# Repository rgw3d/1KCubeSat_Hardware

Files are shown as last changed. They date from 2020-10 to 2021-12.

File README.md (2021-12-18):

# 1KCubeSat_Hardware

Hardware design files for my $1000 cubesat.

Schematics & Layouts are done using KiCad V5.1+

## ½ CubeSat

My progress so far, what I'm calling the ½ Cubesat. The [avionics board](avionics_board) is stacked on the [eps board](eps_board)
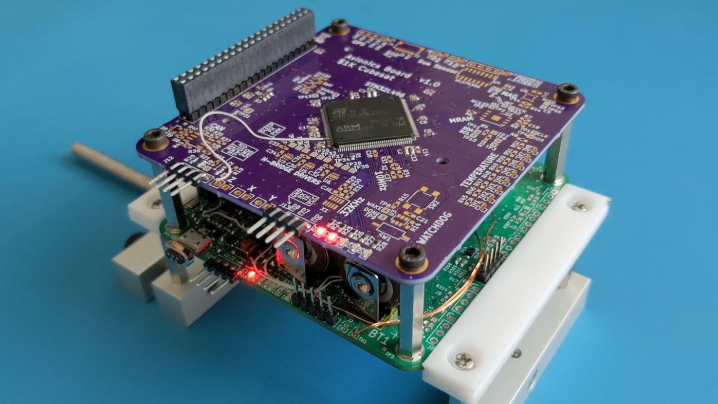
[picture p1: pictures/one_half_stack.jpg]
½ Cubesat Hardware


## Radio Board

See [my fork of the OpenLST repo](https://github.com/rgw3d/openlst-hw/tree/1kcubesat-updates) for more information!
1KCubesat RadioBoard V1

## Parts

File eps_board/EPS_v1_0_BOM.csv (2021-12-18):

Reference | Quantity | Value | Footprint | Datasheet | Mfr. # | Order | Voltage
BT1 BT2 | 2 | Battery_Cell | footprint_custom:BatteryHolder_Keystone_54_v2_1x18650 | https://www.keyelco.com/product.cfm/product_id/826 | 54 | https://www.digikey.com/en/products/detail/keystone-electronics/54/2254090
C1 C2 C13 | 3 | 0.01uF | Capacitor_SMD:C_0603_1608Metric_Pad1.05x0.95mm_HandSolder | ~ | CL10B103KB8NNNC | https://www.digikey.com/en/products/detail/samsung-electro-mechanics/CL10B103KB8NNNC/3886667 | 50V
C4 C5 C6 C7 C8 C9 C10 C11 C12 C16 C17 C18 C19 C20 C21 C24 C26 C29 C31 C36 C38 C47 C49 C50 C53 C55 C57 C58 C61 C63 C65 C66 C69 C71 C73 C74 C77 C79 C81 C82 C85 C87 C89 C90 C93 C95 C97 C98 C101 C103 C105 C106 C109 C111 C113 C114 C117 C119 C121 C122 C125 C127 C129 C130 C133 C135 C137 C138 C141 C143 C145 C146 C149 C151 C153 C154 C157 C159 C161 C162 C165 C167 C169 C170 C173 | 85 | 0.1uF | Capacitor_SMD:C_0603_1608Metric_Pad1.05x0.95mm_HandSolder | ~ | CL10B104KA8NNNC | https://www.digikey.com/product-detail/en/samsung-electro-mechanics/CL10B104KA8NNNC/1276-1006-1-ND/3889092 | 25V
C3 C15 C22 C25 C27 C30 C33 C40 C52 C60 C68 C76 C84 C92 C100 C108 C116 C124 C132 C140 C148 C156 C164 C172 C175 C179 C187 C188 C189 C190 C191 C192 | 32 | 4.7uF | Capacitor_SMD:C_0603_1608Metric_Pad1.05x0.95mm_HandSolder | ~ | C1608X7S1A475K080AC | https://www.digikey.com/product-detail/en/tdk-corporation/C1608X7S1A475K080AC/445-14258-1-ND/3955924 | 10V
C23 C28 C43 C182 | 4 | DNP | Capacitor_SMD:C_0603_1608Metric_Pad1.05x0.95mm_HandSolder | ~
C14 C34 C44 C45 C51 C59 C67 C75 C83 C91 C99 C107 C115 C123 C131 C139 C147 C155 C163 C171 C176 C184 | 22 | 1uF | Capacitor_SMD:C_0603_1608Metric_Pad1.05x0.95mm_HandSolder | ~ | CL10B105KP8NFNC | https://www.digikey.com/product-detail/en/samsung-electro-mechanics/CL10B105KP8NFNC/1276-1945-1-ND/3890031 | 10V
C35 C37 C177 C178 | 4 | 22nF | Capacitor_SMD:C_0603_1608Metric_Pad1.05x0.95mm_HandSolder | ~ | GCM188R72A223KA37D | https://www.digikey.com/product-detail/en/murata-electronics/GCM188R72A223KA37D/490-4782-1-ND/1641701 | 100V
C39 | 1 | 4.7nF | Capacitor_SMD:C_0603_1608Metric_Pad1.05x0.95mm_HandSolder | ~ | 885012206087 | https://www.digikey.com/product-detail/en/w%C3%BCrth-elektronik/885012206087/732-8005-1-ND/5454632 | 50V
C32 C41 C174 C180 C183 C185 | 6 | 47uF | Capacitor_SMD:C_1210_3225Metric_Pad1.42x2.65mm_HandSolder | ~ | GRM32EC81C476KE15L | https://www.digikey.com/product-detail/en/murata-electronics/GRM32EC81C476KE15L/490-10531-1-ND/5026469 | 16V
C42 C181 C186 | 3 | DNP | Capacitor_SMD:C_1210_3225Metric_Pad1.42x2.65mm_HandSolder | ~
C46 C48 C54 C56 C62 C64 C70 C72 C78 C80 C86 C88 C94 C96 C102 C104 C110 C112 C118 C120 C126 C128 C134 C136 C142 C144 C150 C152 C158 C160 C166 C168 | 32 | DNP | Capacitor_SMD:C_0603_1608Metric | ~
D10 D11 D12 D13 D14 D15 D16 D17 | 8 | NRVB120VLSFT1G | footprint_custom:D_SOD-123FL_handsolder | https://www.onsemi.com/pub/Collateral/MBR120VLSFT1-D.PDF | NRVB120VLSFT1G | https://www.digikey.com/product-detail/en/on-semiconductor/NRVB120VLSFT1G/NRVB120VLSFT1GOSCT-ND/8538727
D6 D7 D8 D18 | 4 | ESD9B5.0ST5G | Diode_SMD:D_SOD-923 | https://www.onsemi.com/pub/Collateral/ESD9B-D.PDF | ESD9B5.0ST5G | https://www.digikey.com/product-detail/en/on-semiconductor/ESD9B5-0ST5G/ESD9B5-0ST5GOSCT-ND/1646497
D1 D19 | 2 | LED_SMD_RED | LED_SMD:LED_0603_1608Metric_Pad1.05x0.95mm_HandSolder | https://katalog.we-online.de/led/datasheet/150060RS75000.pdf | 150060RS75000 | https://www.digikey.com/product-detail/en/w%C3%BCrth-elektronik/150060RS75000/732-4978-1-ND/4489899
D2 | 1 | LED_SMD_GREEN | LED_SMD:LED_0603_1608Metric_Pad1.05x0.95mm_HandSolder | https://katalog.we-online.de/led/datasheet/150060VS75000.pdf | 150060VS75000 | https://www.digikey.com/product-detail/en/w%C3%BCrth-elektronik/150060VS75000/732-4980-1-ND/4489904
D3 D4 D5 | 3 | LED_SMD_YELLOW | LED_SMD:LED_0603_1608Metric_Pad1.05x0.95mm_HandSolder | https://www.digikey.com/Web%20Export/Common/icons/datasheet.png | 150060YS75000 | https://www.digikey.com/product-detail/en/w%C3%BCrth-elektronik/150060YS75000/732-4981-1-ND/4489907
D9 | 1 | NUP2105L | Package_TO_SOT_SMD:SOT-23 | http://www.onsemi.com/pub_link/Collateral/NUP2105L-D.PDF | NUP2105LT1G | https://www.digikey.com/product-detail/en/on-semiconductor/NUP2105LT1G/NUP2105LT1GOSCT-ND/1485001
F1 F2 | 2 | Polyfuse | Fuse:Fuse_1206_3216Metric_Pad1.42x1.75mm_HandSolder | ~ | 1206L380SLTHYR | https://www.digikey.com/en/products/detail/littelfuse-inc/1206L380SLTHYR/3305608
FID4 | 1 | Fiducial | Calibration_Scale:Gauge_10mm_Type1_SilkScreenTop | ~
H1 | 1 | MountingHole | MountingHole:MountingHole_2.1mm | ~
H2 H3 H4 H5 | 4 | MountingHole_Pad | MountingHole:MountingHole_3.2mm_M3_Pad_Via | ~
J1 J3 J5 J7 J8 J9 | 6 | Conn_01x04 | Connector_PinHeader_2.54mm:PinHeader_1x04_P2.54mm_Vertical | ~
J12 | 1 | Conn_01x05 | Connector_PinHeader_2.54mm:PinHeader_1x05_P2.54mm_Vertical | ~ | PH1-05-UA | https://www.digikey.com/product-detail/en/adam-tech/PH1-05-UA/2057-PH1-05-UA-ND/9830343
J13 | 1 | Conn_01x04_Male | Connector_PinHeader_2.54mm:PinHeader_1x04_P2.54mm_Vertical | ~ | PREC004SBAN-M71RC | https://www.digikey.com/product-detail/en/sullins-connector-solutions/PREC004SBAN-M71RC/S1112EC-04-ND/2774930
J14 | 1 | USB_B_Micro | Connector_USB:USB_Micro-B_Amphenol_10103594-0001LF_Horizontal | ~ | 10103594-0001LF | https://www.digikey.com/en/products/detail/amphenol-icc-fci/10103594-0001LF/2350351
J2 J4 | 2 | Conn_01x02_Female | Connector_PinHeader_1.27mm:PinHeader_1x02_P1.27mm_Vertical | ~
J6 | 1 | Conn_02x20_Odd_Even | Connector_PinHeader_2.54mm:PinHeader_2x20_P2.54mm_Vertical | ~ | ESQ-120-13-T-D | https://www.digikey.com/product-detail/en/samtec-inc/ESQ-120-13-T-D/ESQ-120-13-T-D-ND/7098677
L1 L2 | 2 | 4.7uH | Inductor_SMD:L_Coilcraft_LPS4018 | ~ | LPS4018-472 | https://www.coilcraft.com/en-us/products/power/shielded-inductors/ferrite-drum/lps/lps4018/
L3 | 1 | 2.2uH | Inductor_SMD:L_Coilcraft_XAL5030 | https://www.coilcraft.com/en-us/products/power/shielded-inductors/molded-inductor/xgl/xgl5030/# | XAL5030-222 | https://www.coilcraft.com/en-us/products/power/shielded-inductors/molded-inductor/xgl/xgl5030/#
Q1 Q2 Q3 Q4 Q5 Q6 Q7 Q8 Q9 Q10 Q11 Q12 Q13 Q14 Q15 Q16 Q17 Q18 Q19 Q20 Q21 Q22 Q23 Q24 Q25 Q26 Q27 Q28 Q29 Q30 Q31 Q32 | 32 | 2N7002K | Package_TO_SOT_SMD:SOT-23 | https://www.diodes.com/assets/Datasheets/ds30896.pdf | 2N7002K-7 | https://www.digikey.com/en/products/detail/diodes-incorporated/2N7002K-7/1934378
R5 R6 R8 R10 R12 R13 R14 R16 R17 R18 R32 R33 R41 R42 R46 R47 R50 R51 R52 R59 R60 R65 R68 R77 R80 R144 R152 R160 R168 R176 R184 R192 R200 R208 R216 R224 R232 R240 R248 R256 R264 R306 R307 R308 R309 R310 R311 R312 R313 R314 R315 R320 | 52 | 100K | Resistor_SMD:R_0603_1608Metric_Pad1.05x0.95mm_HandSolder | ~ | RMCF0603FT100K | https://www.digikey.com/en/products/detail/stackpole-electronics-inc/RMCF0603FT100K/1761112
R101 R103 R105 R123 R125 R127 R129 R135 R137 R139 R141 | 11 | 140K | Resistor_SMD:R_0603_1608Metric_Pad1.05x0.95mm_HandSolder | ~ | RK73H1JTTD1403F | https://www.digikey.com/en/products/detail/koa-speer-electronics-inc/RK73H1JTTD1403F/9845164
R111 R117 | 2 | 698K | Resistor_SMD:R_0603_1608Metric_Pad1.05x0.95mm_HandSolder | ~ | RMCF0603FT698K | https://www.digikey.com/en/products/detail/stackpole-electronics-inc/RMCF0603FT698K/1760941
R113 R115 | 2 | 1.5M | Resistor_SMD:R_0603_1608Metric_Pad1.05x0.95mm_HandSolder | ~ | RC0603FR-071M5L | https://www.digikey.com/en/products/detail/yageo/RC0603FR-071M5L/726865
R15 | 1 | 8.85K | Resistor_SMD:R_0603_1608Metric_Pad1.05x0.95mm_HandSolder | ~ | RMCF0603FT8K87 | https://www.digikey.com/product-detail/en/stackpole-electronics-inc/RMCF0603FT8K87/RMCF0603FT8K87CT-ND/1943053
R19 R20 R21 R22 R23 | 5 | 49.9 | Resistor_SMD:R_0603_1608Metric_Pad1.05x0.95mm_HandSolder | https://www.mouser.com/datasheet/2/392/susumu_RR_Data_Sheet-1206438.pdf | RR0816Q-49R9-D-68R | https://www.mouser.com/ProductDetail/Susumu/RR0816Q-49R9-D-68R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
R322 | 1 | 137K | Resistor_SMD:R_0603_1608Metric_Pad1.05x0.95mm_HandSolder | ~ | RMCF0603FT137K | https://www.digikey.com/en/products/detail/stackpole-electronics-inc/RMCF0603FT137K/1713607
R323 R324 R325 R326 | 4 | 1 | Resistor_SMD:R_0603_1608Metric_Pad1.05x0.95mm_HandSolder | ~ | RK73H1JTTD1R00F | https://www.digikey.com/en/products/detail/koa-speer-electronics-inc/RK73H1JTTD1R00F/9844862
R1 R29 R30 R31 R35 R36 R37 R38 R57 R58 R87 R88 R89 R90 R143 R149 R151 R157 R159 R165 R167 R173 R175 R181 R183 R189 R191 R197 R199 R205 R207 R213 R215 R221 R223 R229 R231 R237 R239 R245 R247 R253 R255 R261 R263 R269 R304 R305 R316 R317 R318 R319 R327 | 53 | 0 | Resistor_SMD:R_0603_1608Metric_Pad1.05x0.95mm_HandSolder | ~ | RK73Z1JTTD | https://www.digikey.com/product-detail/en/koa-speer-electronics-inc/RK73Z1JTTD/2019-RK73Z1JTTDCT-ND/9847522
R24 R25 R26 R27 R28 R329 | 6 | 330 | Resistor_SMD:R_0603_1608Metric_Pad1.05x0.95mm_HandSolder | https://www.mouser.com/datasheet/2/427/dcrcwe3-1762152.pdf | CRCW0603330RJNEA | https://www.mouser.com/ProductDetail/Vishay-Dale/CRCW0603330RJNEA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
R39 R40 | 2 | 60.4 | Resistor_SMD:R_0603_1608Metric_Pad1.05x0.95mm_HandSolder | ~ | RMCF0603FT60R4 | https://www.digikey.com/product-detail/en/stackpole-electronics-inc/RMCF0603FT60R4/RMCF0603FT60R4CT-ND/2418105
R34 R43 | 2 | 150K | Resistor_SMD:R_0603_1608Metric_Pad1.05x0.95mm_HandSolder | ~ | RMCF0603FT150K | https://www.digikey.com/en/products/detail/stackpole-electronics-inc/RMCF0603FT150K/1761318
R11 R48 R62 R64 R66 R67 R74 R76 R78 R79 R97 R98 | 12 | 10K | Resistor_SMD:R_0603_1608Metric_Pad1.05x0.95mm_HandSolder | ~ | RMCF0603FT10K0 | https://www.digikey.com/en/products/detail/stackpole-electronics-inc/RMCF0603FT10K0/1761235
R2 R3 R4 R7 R49 R53 R54 R55 R56 R328 | 10 | 10m | Resistor_SMD:R_0603_1608Metric_Pad1.05x0.95mm_HandSolder | ~ | ERJ-3LWJR010V | https://www.digikey.com/product-detail/en/panasonic-electronic-components/ERJ-3LWJR010V/P19190CT-ND/6004545
R61 R73 | 2 | 26.7K | Resistor_SMD:R_0603_1608Metric_Pad1.05x0.95mm_HandSolder | ~ | RK73H1JTTD2672F | https://www.digikey.com/en/products/detail/koa-speer-electronics-inc/RK73H1JTTD2672F/9845116
R63 R71 R75 R83 R145 R147 R148 R153 R155 R156 R161 R163 R164 R169 R171 R172 R177 R179 R180 R185 R187 R188 R193 R195 R196 R201 R203 R204 R209 R211 R212 R217 R219 R220 R225 R227 R228 R233 R235 R236 R241 R243 R244 R249 R251 R252 R257 R259 R260 R265 R267 R268 R321 | 53 | 1M | Resistor_SMD:R_0603_1608Metric_Pad1.05x0.95mm_HandSolder | ~ | RMCF0603JT1M00 | https://www.digikey.com/en/products/detail/stackpole-electronics-inc/RMCF0603JT1M00/1758066
R69 R81 | 2 | 280K | Resistor_SMD:R_0603_1608Metric_Pad1.05x0.95mm_HandSolder | ~ | RMCF0603FT280K | https://www.digikey.com/en/products/detail/stackpole-electronics-inc/RMCF0603FT280K/1761337
R70 R82 R150 R158 R166 R174 R182 R190 R198 R206 R214 R222 R230 R238 R246 R254 R262 R270 | 18 | DNP | Resistor_SMD:R_0603_1608Metric_Pad1.05x0.95mm_HandSolder | ~
R72 R84 R100 R102 R104 R106 R112 R114 R116 R118 R124 R126 R128 R130 R136 R138 R140 R142 | 18 | 3.09K | Resistor_SMD:R_0603_1608Metric_Pad1.05x0.95mm_HandSolder | ~ | RMCF0603FT3K09 | https://www.digikey.com/en/products/detail/stackpole-electronics-inc/RMCF0603FT3K09/1761340
R85 R86 | 2 | 150 | Resistor_SMD:R_0603_1608Metric_Pad1.05x0.95mm_HandSolder | ~ | RMCF0603JT150R | https://www.digikey.com/en/products/detail/stackpole-electronics-inc/RMCF0603JT150R/1757965
R9 | 1 | 224K | Resistor_SMD:R_0603_1608Metric_Pad1.05x0.95mm_HandSolder | ~ | RMCF0603FT221K | https://www.digikey.com/en/products/detail/stackpole-electronics-inc/RMCF0603FT221K/1760806
R91 R92 | 2 | 1K | Resistor_SMD:R_0603_1608Metric_Pad1.05x0.95mm_HandSolder | ~ | RMCF0603FT1K00 | https://www.digikey.com/en/products/detail/stackpole-electronics-inc/RMCF0603FT1K00/1761077
R93 R95 R96 R107 R108 R109 R110 R119 R120 R121 R122 R131 R132 R133 R134 | 15 | 0.1 | Resistor_SMD:R_0603_1608Metric_Pad1.05x0.95mm_HandSolder | ~ | ERJ-3RSFR10V | https://www.digikey.com/product-detail/en/panasonic-electronic-components/ERJ-3RSFR10V/P-10AJCT-ND/308098
R94 | 1 | 0.039 | Resistor_SMD:R_0603_1608Metric_Pad1.05x0.95mm_HandSolder | ~ | ERJ-3BWFR039V | https://www.digikey.com/en/products/detail/panasonic-electronic-components/ERJ-3BWFR039V/5647502
R99 | 1 | 20K | Resistor_SMD:R_0603_1608Metric_Pad1.05x0.95mm_HandSolder | ~ | RMCF0603FT20K0 | https://www.digikey.com/en/products/detail/stackpole-electronics-inc/RMCF0603FT20K0/1760829
SW1 | 1 | SW_DIP_x01 | Button_Switch_SMD:SW_DIP_SPSTx01_Slide_Copal_CHS-01B_W7.62mm_P1.27mm | https://www.nidec-copal-electronics.com/e/catalog/switch/chs.pdf | CHS-01TB | https://www.digikey.com/product-detail/en/nidec-copal-electronics/CHS-01TB/563-1004-1-ND/948403
SW2 | 1 | SW_Push | Button_Switch_SMD:SW_SPST_TL3305A | https://sten-eswitch-13110800-production.s3.amazonaws.com/system/asset/product_line/data_sheet/213/TL3305.pdf | TL3305AF260QG | https://www.digikey.com/product-detail/en/e-switch/TL3305AF260QG/EG5353CT-ND/5816198
TH1 TH2 | 2 | Thermistor_NTC | Connector_PinHeader_1.27mm:PinHeader_1x02_P1.27mm_Vertical | ~ | NXFT15XH103FA2B130 | https://www.digikey.com/en/products/detail/murata-electronics/NXFT15XH103FA2B130/3863299
TP37 TP39 | 2 | TP_1.5x1.5 | TestPoint:TestPoint_THTPad_1.0x1.0mm_Drill0.5mm | ~
TP7 TP10 TP11 TP12 TP13 TP14 TP15 TP16 TP17 TP18 TP19 TP20 | 12 | TP_1x1 | TestPoint:TestPoint_THTPad_1.0x1.0mm_Drill0.5mm | ~
TP1 TP2 TP3 TP4 TP5 TP8 TP9 | 7 | TP_smt_1x1 | TestPoint:TestPoint_THTPad_1.0x1.0mm_Drill0.5mm | ~
U1 | 1 | STM32L496ZGTx | Package_QFP:LQFP-144_20x20mm_P0.5mm | http://www.st.com/st-web-ui/static/active/en/resource/technical/document/datasheet/DM00284211.pdf | STM32L496ZGT3 | https://www.digikey.com/product-detail/en/stmicroelectronics/STM32L496ZGT3/497-17177-ND/6709882
U10 U13 | 2 | MCP65R46 | Package_TO_SOT_SMD:SOT-23-6_Handsoldering | http://ww1.microchip.com/downloads/en/DeviceDoc/22269B.pdf | MCP65R46T-2402E/CHY | https://www.digikey.com/product-detail/en/microchip-technology/MCP65R46T-2402E-CHY/MCP65R46T-2402E-CHYCT-ND/2618485
U11 U14 U22 U26 U30 U34 U38 U42 U46 U50 U54 U58 U62 U66 U70 U74 U78 U82 | 18 | FPF2123 | Package_TO_SOT_SMD:SOT-23-5_HandSoldering | https://www.onsemi.com/pub/Collateral/FPF2125-D.pdf | FPF2123 | https://www.digikey.com/product-detail/en/on-semiconductor/FPF2123/FPF2123CT-ND/1033703
U15 | 1 | LTC4415 | footprint_custom:MSOP-16-1EP_3x4.039mm_P0.5mm_EP1.651x2.845mm_0.3mmThermalVias | https://www.analog.com/media/en/technical-documentation/data-sheets/4415fa.pdf | LTC4415EMSE#PBF | https://www.digikey.com/product-detail/en/analog-devices-inc/LTC4415EMSE-PBF/LTC4415EMSE-PBF-ND/2769860
U16 U83 | 2 | LTC3130-1 | footprint_custom:MSOP-16-1EP_3x4.039mm_P0.5mm_EP1.651x2.845mm_0.3mmThermalVias | https://www.analog.com/media/en/technical-documentation/data-sheets/3130f.pdf | LTC3130EMSE-1#PBF | https://www.digikey.com/product-detail/en/analog-devices-inc/LTC3130EMSE-1-PBF/LTC3130EMSE-1-PBF-ND/6174043
U19 U23 U27 U31 U35 U39 U43 U47 U51 U55 U59 U63 U67 U71 U75 U79 | 16 | NCS211 | Package_TO_SOT_SMD:SOT-363_SC-70-6 | https://www.onsemi.com/pub/Collateral/NCS210R-D.PDF | NCS214RSQT2G | https://www.digikey.com/product-detail/en/on-semiconductor/NCS214RSQT2G/NCS214RSQT2GOSCT-ND/9749437
U2 | 1 | MR25H10 | Package_DFN_QFN:DFN-8-1EP_6x5mm_P1.27mm_EP2x2mm | https://media.digikey.com/pdf/Data%20Sheets/EverSpin%20Technologies/MR25H40_Datasheet_Rev6.pdf | MR25H10MDF | https://www.digikey.com/product-detail/en/everspin-technologies-inc/MR25H10MDF/819-1042-ND/4047457
U20 U24 U28 U32 U36 U40 U44 U48 U52 U56 U60 U64 U68 U72 U76 U80 | 16 | 74LVC1G07 | Package_TO_SOT_SMD:SOT-353_SC-70-5 | https://assets.nexperia.com/documents/data-sheet/74LVC1G07.pdf | 74LVC1G07GW,125 | https://www.digikey.com/product-detail/en/nexperia-usa-inc/74LVC1G07GW-125/1727-3099-1-ND/946756
U21 U25 U29 U33 U37 U41 U45 U49 U53 U57 U61 U65 U69 U73 U77 U81 | 16 | MCP65R46 | Package_TO_SOT_SMD:SOT-23-6 | http://ww1.microchip.com/downloads/en/DeviceDoc/22269B.pdf | MCP65R46T-2402E/CHY | https://www.digikey.com/product-detail/en/microchip-technology/MCP65R46T-2402E-CHY/MCP65R46T-2402E-CHYCT-ND/2618485
U3 | 1 | TPL5010 | Package_TO_SOT_SMD:SOT-23-6 | http://www.ti.com/lit/ds/symlink/tpl5010.pdf | TPL5010DDCR | https://www.digikey.com/product-detail/en/texas-instruments/TPL5010DDCR/296-44392-1-ND/6110660
U4 U5 U17 U18 | 4 | TPS270 | Package_TO_SOT_SMD:TSOT-23-6_HandSoldering | https://www.ti.com/lit/ds/symlink/tps27081a.pdf?HQS=TI-null-null-digikeymode-df-pf-null-wwe&ts=1599272332553 | TPS27081ADDCR | https://www.digikey.com/product-detail/en/texas-instruments/TPS27081ADDCR/296-34970-1-ND/3671576
U6 U7 | 2 | 74LVC1G07 | Package_TO_SOT_SMD:SOT-353_SC-70-5_Handsoldering | http://www.ti.com/lit/sg/scyt129e/scyt129e.pdf | 74LVC1G07GW,125 | https://www.digikey.com/product-detail/en/nexperia-usa-inc/74LVC1G07GW-125/1727-3099-1-ND/946756
U8 | 1 | SN65HVD230 | Package_SO:SOIC-8_3.9x4.9mm_P1.27mm | http://www.ti.com/lit/ds/symlink/sn65hvd230.pdf | SN65HVD230QDRG4Q1 | https://www.digikey.com/product-detail/en/texas-instruments/SN65HVD230QDG4/296-26342-5-ND/1900402
U84 | 1 | MP3414A | Package_TO_SOT_SMD:TSOT-23-8_HandSoldering | https://www.monolithicpower.com/en/documentview/productdocument/index/version/2/document_type/Datasheet/lang/en/sku/MP3414A/document_id/1172/ | MP3414AGJ-Z | https://www.digikey.com/en/products/detail/monolithic-power-systems-inc/MP3414AGJ-Z/7361472
U9 U12 | 2 | LTC4066 | footprint_custom:QFN-24-1EP_4x4mm_P0.5mm_EP2.6x2.6mm_0.4mmThermalVias | https://www.analog.com/media/en/technical-documentation/data-sheets/4066fc.pdf | LTC4066EUF#PBF | https://www.digikey.com/product-detail/en/analog-devices-inc/LTC4066EUF-PBF/LTC4066EUF-PBF-ND/1746224
X1 | 1 | TG-3541CE | footprint_custom:Oscillator_SMD_SeikoEpson_TG3541CE-10Pin_3.2x2.5mm_HandSoldering | https://support.epson.biz/td/api/doc_check.php?dl=brief_TG-3541CE&lang=en | TG-3541CE 32.7680KXA3 | https://www.digikey.com/product-detail/en/epson/TG-3541CE-32-7680KXA3/SER4421CT-ND/10239844

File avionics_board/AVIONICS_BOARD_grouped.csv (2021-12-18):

Reference | Quantity | Value | Footprint | Datasheet | Mfr. # | Order | Voltage | Alt
C1 C2 C13 | 3 | 0.01uF | Capacitor_SMD:C_0603_1608Metric_Pad1.08x0.95mm_HandSolder | ~ | CL10B103KB8NNNC | https://www.digikey.com/en/products/detail/samsung-electro-mechanics/CL10B103KB8NNNC/3886667 | 50V
C14 C28 C44 | 3 | 1uF | Capacitor_SMD:C_0603_1608Metric_Pad1.08x0.95mm_HandSolder | ~ | CL10B105KP8NFNC | https://www.digikey.com/product-detail/en/samsung-electro-mechanics/CL10B105KP8NFNC/1276-1945-1-ND/3890031 | 10V
C3 C15 | 2 | 4.7uF | Capacitor_SMD:C_0603_1608Metric_Pad1.08x0.95mm_HandSolder | ~ | C1608X7S1A475K080AC | https://www.digikey.com/product-detail/en/tdk-corporation/C1608X7S1A475K080AC/445-14258-1-ND/3955924 | 10V
C39 | 1 | 4.7nF | Capacitor_SMD:C_0603_1608Metric_Pad1.08x0.95mm_HandSolder | ~ | 885012206087 | https://www.digikey.com/product-detail/en/w%C3%BCrth-elektronik/885012206087/732-8005-1-ND/5454632 | 50V
C45 | 1 | 10uF | Capacitor_SMD:C_0603_1608Metric_Pad1.08x0.95mm_HandSolder | ~ | CL10X106MO8NRNC | https://www.digikey.com/product-detail/en/samsung-electro-mechanics/CL10X106MO8NRNC/1276-6769-1-ND/5961628 | 16V
C4 C5 C6 C7 C8 C9 C10 C11 C12 C16 C17 C18 C19 C20 C21 C29 C30 C31 C32 C33 C34 C35 C36 C37 C38 C40 C43 | 27 | 0.1uF | Capacitor_SMD:C_0603_1608Metric_Pad1.08x0.95mm_HandSolder | ~ | CL10B104KA8NNNC | https://www.digikey.com/product-detail/en/samsung-electro-mechanics/CL10B104KA8NNNC/1276-1006-1-ND/3889092 | 25V
D1 | 1 | LED_SMD_RED | LED_SMD:LED_0603_1608Metric_Pad1.05x0.95mm_HandSolder | https://katalog.we-online.de/led/datasheet/150060RS75000.pdf | 150060RS75000 | https://www.digikey.com/product-detail/en/w%C3%BCrth-elektronik/150060RS75000/732-4978-1-ND/4489899
D2 | 1 | LED_SMD_GREEN | LED_SMD:LED_0603_1608Metric_Pad1.05x0.95mm_HandSolder | https://katalog.we-online.de/led/datasheet/150060VS75000.pdf | 150060VS75000 | https://www.digikey.com/product-detail/en/w%C3%BCrth-elektronik/150060VS75000/732-4980-1-ND/4489904
D3 D4 D5 | 3 | LED_SMD_YELLOW | LED_SMD:LED_0603_1608Metric_Pad1.05x0.95mm_HandSolder | https://www.digikey.com/Web%20Export/Common/icons/datasheet.png | 150060YS75000 | https://www.digikey.com/product-detail/en/w%C3%BCrth-elektronik/150060YS75000/732-4981-1-ND/4489907
D6 D7 D8 | 3 | ESD9B5.0ST5G | Diode_SMD:D_SOD-923 | https://www.onsemi.com/pub/Collateral/ESD9B-D.PDF | ESD9B5.0ST5G | https://www.digikey.com/product-detail/en/on-semiconductor/ESD9B5-0ST5G/ESD9B5-0ST5GOSCT-ND/1646497
D9 | 1 | NUP2105L | Package_TO_SOT_SMD:SOT-23 | http://www.onsemi.com/pub_link/Collateral/NUP2105L-D.PDF | NUP2105LT1G | https://www.digikey.com/product-detail/en/on-semiconductor/NUP2105LT1G/NUP2105LT1GOSCT-ND/1485001
H1 H2 H3 H4 | 4 | MountingHole_Pad | MountingHole:MountingHole_3.2mm_M3_Pad_Via | ~
H5 H6 H7 | 3 | MountingHole | MountingHole:MountingHole_2.7mm | ~
J1 | 1 | Conn_02x20_Odd_Even | Connector_PinHeader_2.54mm:PinHeader_2x20_P2.54mm_Vertical | ~ | ESQ-120-13-T-D | https://www.digikey.com/product-detail/en/samtec-inc/ESQ-120-13-T-D/ESQ-120-13-T-D-ND/7098677
J13 | 1 | Conn_01x04_Male | Connector_PinHeader_2.54mm:PinHeader_1x04_P2.54mm_Vertical | ~ | PREC004SBAN-M71RC | https://www.digikey.com/product-detail/en/sullins-connector-solutions/PREC004SBAN-M71RC/S1112EC-04-ND/2774930
J3 | 1 | JST socket 6-pin 1mm pitch JST SH SM06B-SRSS-TB | Connector_JST:JST_SH_SM06B-SRSS-TB_1x06-1MP_P1.00mm_Horizontal | ~ | SM06B-SRSS-TB(LF)(SN) | https://www.digikey.com/product-detail/en/jst-sales-america-inc/SM06B-SRSS-TB-LF-SN/455-1806-1-ND/926877
J4 J7 J12 | 3 | Conn_01x05 | Connector_PinHeader_2.54mm:PinHeader_1x05_P2.54mm_Vertical | ~ | PH1-05-UA | https://www.digikey.com/product-detail/en/adam-tech/PH1-05-UA/2057-PH1-05-UA-ND/9830343
J5 J6 J9 J10 J11 | 5 | Conn_01x02 | Connector_PinHeader_2.54mm:PinHeader_1x02_P2.54mm_Vertical | ~ | PREC002SAAN-RC | https://www.digikey.com/product-detail/en/sullins-connector-solutions/PREC002SAAN-RC/S1012EC-02-ND/2774852
R1 R8 R16 R17 R18 R29 R30 R31 R32 R33 R34 R35 R36 R37 R38 R42 R43 R44 | 18 | 0 | Resistor_SMD:R_0603_1608Metric_Pad0.98x0.95mm_HandSolder | ~ | RK73Z1JTTD | https://www.digikey.com/product-detail/en/koa-speer-electronics-inc/RK73Z1JTTD/2019-RK73Z1JTTDCT-ND/9847522
R9 R10 R11 R12 | 4 | DNP | Resistor_SMD:R_0603_1608Metric_Pad0.98x0.95mm_HandSolder | ~
R15 | 1 | 8.85K | Resistor_SMD:R_0603_1608Metric_Pad0.98x0.95mm_HandSolder | ~ | RMCF0603FT8K87 | https://www.digikey.com/product-detail/en/stackpole-electronics-inc/RMCF0603FT8K87/RMCF0603FT8K87CT-ND/1943053
R2 R3 R4 R7 | 4 | 10m | Resistor_SMD:R_0603_1608Metric_Pad0.98x0.95mm_HandSolder | ~ | ERJ-3LWJR010V | https://www.digikey.com/product-detail/en/panasonic-electronic-components/ERJ-3LWJR010V/P19190CT-ND/6004545
R19 R20 R21 R22 R23 | 5 | 49.9 | Resistor_SMD:R_0603_1608Metric_Pad0.98x0.95mm_HandSolder | https://www.mouser.com/datasheet/2/392/susumu_RR_Data_Sheet-1206438.pdf | RR0816Q-49R9-D-68R | https://www.mouser.com/ProductDetail/Susumu/RR0816Q-49R9-D-68R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
R24 R25 R26 R27 R28 | 5 | 330 | Resistor_SMD:R_0603_1608Metric_Pad0.98x0.95mm_HandSolder | https://www.mouser.com/datasheet/2/427/dcrcwe3-1762152.pdf | CRCW0603330RJNEA | https://www.mouser.com/ProductDetail/Vishay-Dale/CRCW0603330RJNEA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
R39 R40 | 2 | 60.4 | Resistor_SMD:R_0603_1608Metric_Pad0.98x0.95mm_HandSolder | ~ | RMCF0603FT60R4 | https://www.digikey.com/product-detail/en/stackpole-electronics-inc/RMCF0603FT60R4/RMCF0603FT60R4CT-ND/2418105
R45 R46 R47 R48 R49 R50 R51 R52 | 8 | 47K | Resistor_SMD:R_0603_1608Metric_Pad0.98x0.95mm_HandSolder | https://www.bourns.com/docs/Product-Datasheets/CHPREZTR.pdf | CR0603-FX-4702ELF | https://www.digikey.com/product-detail/en/bourns-inc/CR0603-FX-4702ELF/CR0603-FX-4702ELFCT-ND/3925317
R5 R6 R14 R41 | 4 | 100K | Resistor_SMD:R_0603_1608Metric_Pad0.98x0.95mm_HandSolder | ~ | RMCF0603FT100K | https://www.digikey.com/en/products/detail/stackpole-electronics-inc/RMCF0603FT100K/1761112
SW1 | 1 | SW_DIP_x01 | Button_Switch_SMD:SW_DIP_SPSTx01_Slide_Copal_CHS-01B_W7.62mm_P1.27mm | https://www.nidec-copal-electronics.com/e/catalog/switch/chs.pdf | CHS-01TB | https://www.digikey.com/product-detail/en/nidec-copal-electronics/CHS-01TB/563-1004-1-ND/948403
SW2 | 1 | SW_Push | Button_Switch_SMD:SW_SPST_TL3305A | https://sten-eswitch-13110800-production.s3.amazonaws.com/system/asset/product_line/data_sheet/213/TL3305.pdf | TL3305AF260QG | https://www.digikey.com/product-detail/en/e-switch/TL3305AF260QG/EG5353CT-ND/5816198
TH1 TH2 TH3 TH4 TH5 TH6 TH7 TH8 | 8 | Thermistor_NTC | Connector_PinHeader_1.27mm:PinHeader_1x02_P1.27mm_Vertical | https://www.murata.com/~/media/webrenewal/support/library/catalog/products/thermistor/ntc/r44e.ashx?la=en-us | NXFT15WB473FA2B150 | https://www.digikey.com/product-detail/en/murata-electronics/NXFT15WB473FA2B150/490-14853-ND/6606459
TP7 TP10 TP11 TP12 TP13 | 5 | TP_tht_1x1 | TestPoint:TestPoint_THTPad_1.0x1.0mm_Drill0.5mm | ~
TP14 TP15 TP16 TP26 TP27 TP28 TP29 TP30 TP33 TP34 TP35 TP36 TP43 TP44 TP45 TP48 TP49 TP50 TP52 TP53 TP54 TP56 TP57 | 23 | TP_smt_1x1 | TestPoint:TestPoint_Pad_1.0x1.0mm | ~
TP1 TP2 TP3 TP4 TP5 TP6 TP8 TP9 | 8 | TP_smt_1x1 | TestPoint:TestPoint_THTPad_1.0x1.0mm_Drill0.5mm | ~
TP31 TP32 | 2 | TP_1.5x1.5 | TestPoint:TestPoint_THTPad_1.5x1.5mm_Drill0.7mm | ~
TP37 TP39 | 2 | TP_1.5x1.5 | TestPoint:TestPoint_THTPad_1.0x1.0mm_Drill0.5mm | ~
U1 | 1 | STM32L496ZGTx | Package_QFP:LQFP-144_20x20mm_P0.5mm | http://www.st.com/st-web-ui/static/active/en/resource/technical/document/datasheet/DM00284211.pdf | STM32L496ZGT3 | https://www.digikey.com/product-detail/en/stmicroelectronics/STM32L496ZGT3/497-17177-ND/6709882
U10 | 1 | BMG250 | Package_LGA:Bosch_LGA-14_3x2.5mm_P0.5mm | https://ae-bst.resource.bosch.com/media/_tech/media/datasheets/BST-BMG250-DS000.pdf | BMG250 | https://www.digikey.com/product-detail/en/bosch-sensortec/BMG250/828-1065-1-ND/6187900
U11 U12 | 2 | 74LVC1G07 | Package_TO_SOT_SMD:SOT-353_SC-70-5_Handsoldering | http://www.ti.com/lit/sg/scyt129e/scyt129e.pdf | 74LVC1G07GW,125 | https://www.digikey.com/product-detail/en/nexperia-usa-inc/74LVC1G07GW-125/1727-3099-1-ND/946756 |  | https://www.digikey.com/product-detail/en/texas-instruments/SN74LVC1G07DCKR/296-8486-1-ND/377456
U2 | 1 | MR25H10 | Package_DFN_QFN:DFN-8-1EP_6x5mm_P1.27mm_EP2x2mm | https://media.digikey.com/pdf/Data%20Sheets/EverSpin%20Technologies/MR25H40_Datasheet_Rev6.pdf | MR25H10MDF | https://www.digikey.com/product-detail/en/everspin-technologies-inc/MR25H10MDF/819-1042-ND/4047457
U3 | 1 | TPL5010 | Package_TO_SOT_SMD:SOT-23-6 | http://www.ti.com/lit/ds/symlink/tpl5010.pdf | TPL5010DDCR | https://www.digikey.com/product-detail/en/texas-instruments/TPL5010DDCR/296-44392-1-ND/6110660
U4 | 1 | MLX75306 | Package_SO:SOIC-16_3.9x9.9mm_P1.27mm |  | MLX75306KXZ-BAA-000-RE | https://www.digikey.com/product-detail/en/melexis-technologies-nv/MLX75306KXZ-BAA-000-RE/MLX75306KXZ-BAA-000-RECT-ND/3640931
U5 U6 U7 | 3 | DRV8838 | Package_SON:WSON-8-1EP_2x2mm_P0.5mm_EP0.9x1.6mm | http://www.ti.com/lit/ds/symlink/drv8837.pdf | DRV8838DSGR | https://www.digikey.com/product-detail/en/texas-instruments/DRV8838DSGR/296-40081-1-ND/5177958
U8 | 1 | SN65HVD230 | Package_SO:SOIC-8_3.9x4.9mm_P1.27mm | http://www.ti.com/lit/ds/symlink/sn65hvd230.pdf | SN65HVD230QDRG4Q1 | https://www.digikey.com/product-detail/en/texas-instruments/SN65HVD230QDG4/296-26342-5-ND/1900402
U9 | 1 | MMC5983MA | Package_LGA:LGA-16_3x3mm_P0.5mm | https://media.digikey.com/pdf/Data%20Sheets/MEMSIC%20PDFs/MMC5983MA_RevA_4-3-19.pdf | MMC5983MA | https://www.digikey.com/product-detail/en/memsic-inc/MMC5983MA/1267-MMC5983MACT-ND/10452801
X1 | 1 | TG-3541CE | footprint_custom:Oscillator_SMD_SeikoEpson_TG3541CE-10Pin_3.2x2.5mm_HandSoldering | https://support.epson.biz/td/api/doc_check.php?dl=brief_TG-3541CE&lang=en | TG-3541CE 32.7680KXA3 | https://www.digikey.com/product-detail/en/epson/TG-3541CE-32-7680KXA3/SER4421CT-ND/10239844
X2 | 1 | ECS-TXO-2016 | footprint_custom:Oscillator_SMD_ECS_TXO-2016-xx-xxx-4Pin_2.0x1.6mm | https://ecsxtal.com/store/pdf/ECS-TXO-2016.pdf | ECS-TXO-2016-33-100-TR | https://www.digikey.com/product-detail/en/ecs-inc/ECS-TXO-2016-33-100-TR/XC3159CT-ND/10244142

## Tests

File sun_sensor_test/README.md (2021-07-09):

# Sun Sensor Test

Testing out a potential sun sensor using the K857PE 4-Quadrent Photodiode. See the [pdf](https://raw.githubusercontent.com/rgw3d/1KCubeSat_Hardware/master/sun_sensor_test/sun_sensor_test.pdf) for more information.

See [my video on this board](https://www.youtube.com/watch?v=8ttuiI6RIH0) for more information.

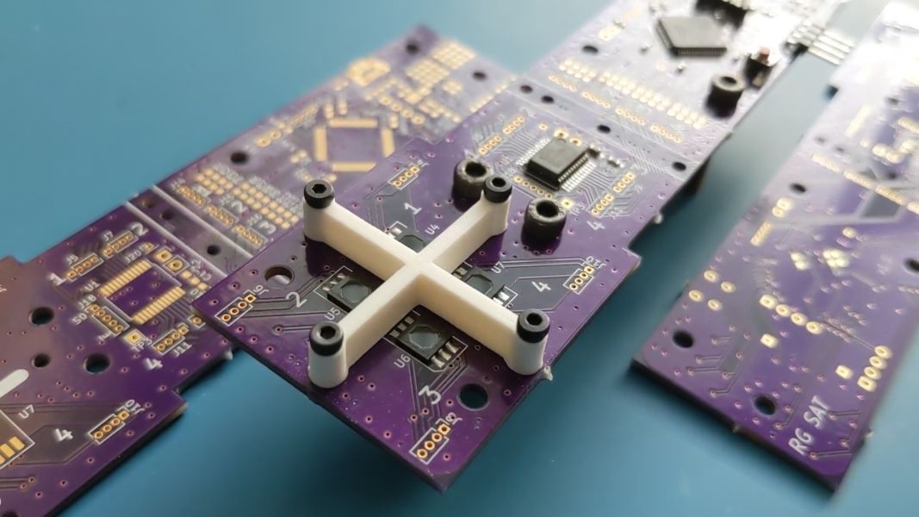
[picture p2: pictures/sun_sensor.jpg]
Sun Sensor Hardware


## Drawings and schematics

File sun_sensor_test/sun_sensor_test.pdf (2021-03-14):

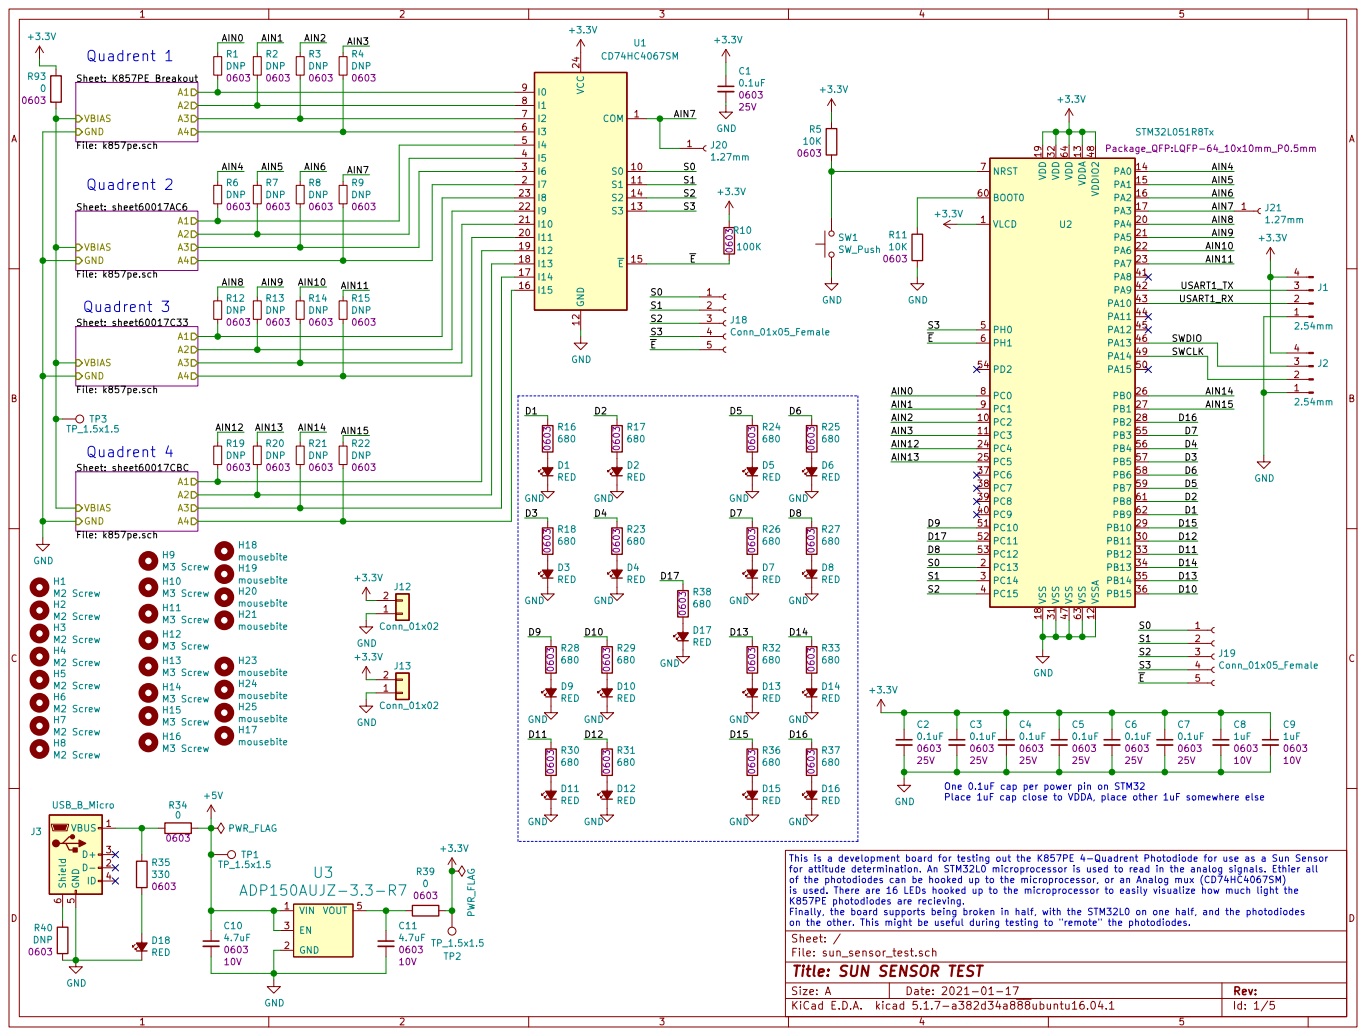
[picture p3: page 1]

Sheet: K857PE Breakout File: k857pe.sch GND
A1A2A3A4 VBIAS
25V H6M2 Screw

Sheet: sheet60017AC6 File: k857pe.sch GND

Quadrent 3
Sheet: sheet60017C33 File: k857pe.sch GND

One 0.1uF cap per power pin on STM32
Place 1uF cap close to VDDA, place other 1uF somewhere else

for attitude determination. An STM32L0 microprocessor is used to read in the analog signals. Ethier all
of the photodiodes can be hooked up to the microprocessor, or an Analog mux (CD74HC4067SM)
is used. There are 16 LEDs hooked up to the microprocessor to easily visualize how much light the
K857PE photodiodes are recieving.
Finally, the board supports being broken in half, with the STM32L0 on one half, and the photodiodes
on the other. This might be useful during testing to "remote" the photodiodes.
File: sun_sensor_test.sch Sheet: /
Id: 1/5 Title: SUN SENSOR TEST

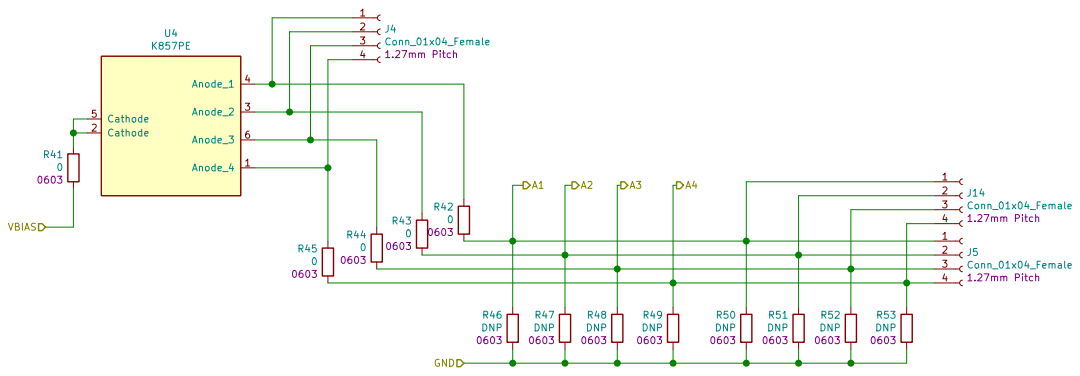
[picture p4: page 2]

File: k857pe.sch Sheet: /K857PE Breakout/
Id: 2/5 Title: K857PE

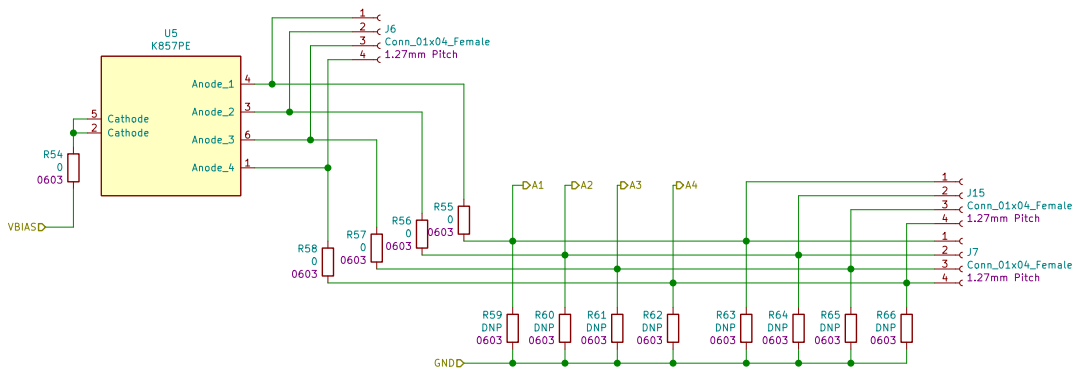
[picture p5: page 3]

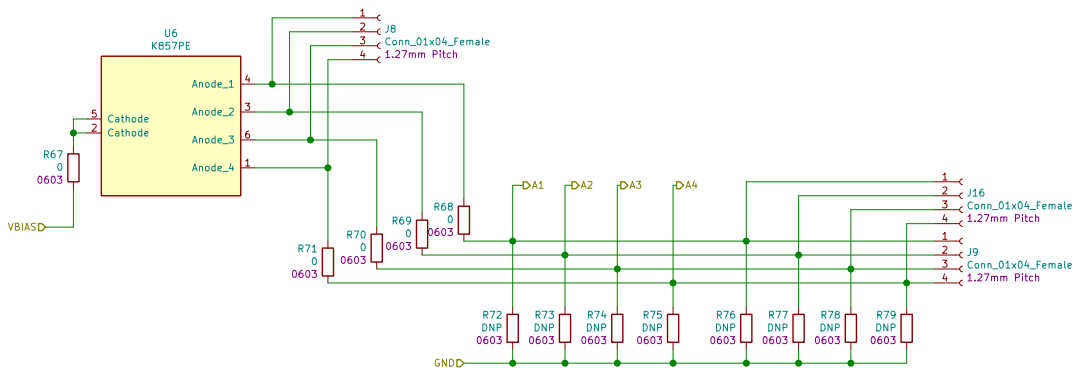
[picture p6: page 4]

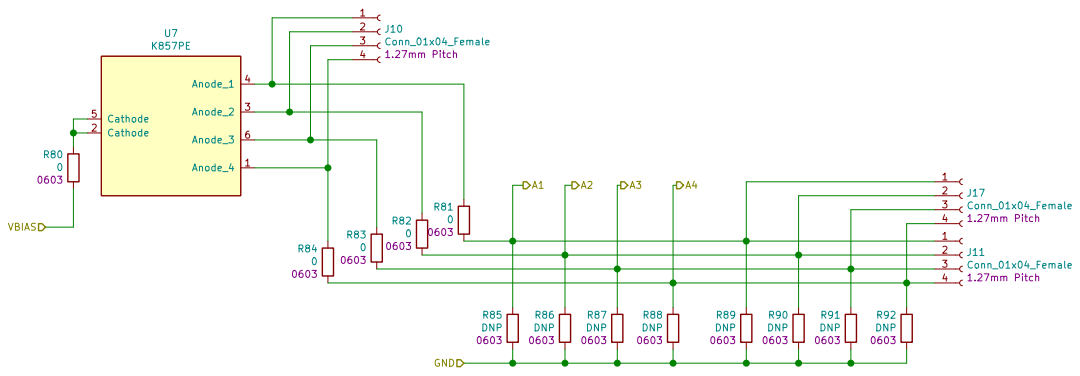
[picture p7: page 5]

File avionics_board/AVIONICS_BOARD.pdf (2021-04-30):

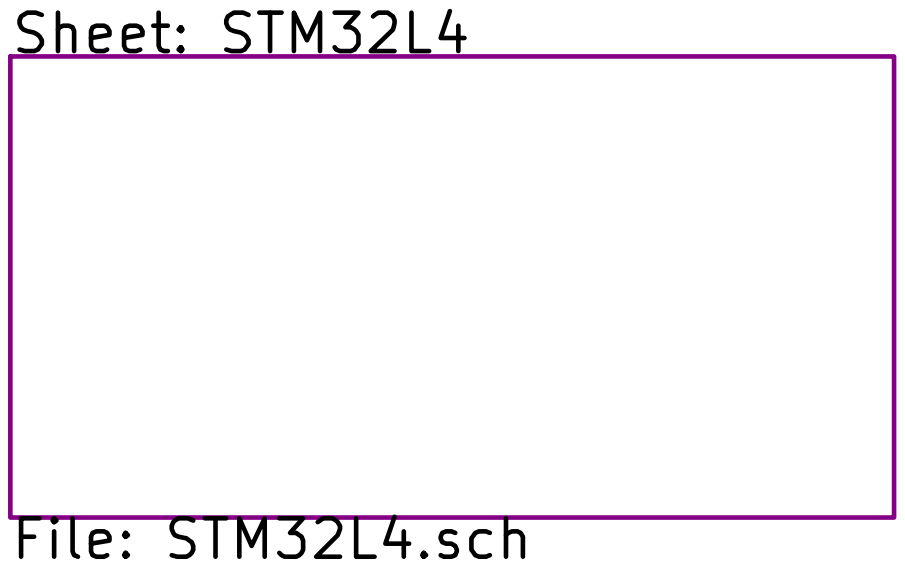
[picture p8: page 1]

File: AVIONICS_BOARD.sch Sheet: / Sheet: STM32L4 File: STM32L4.sch

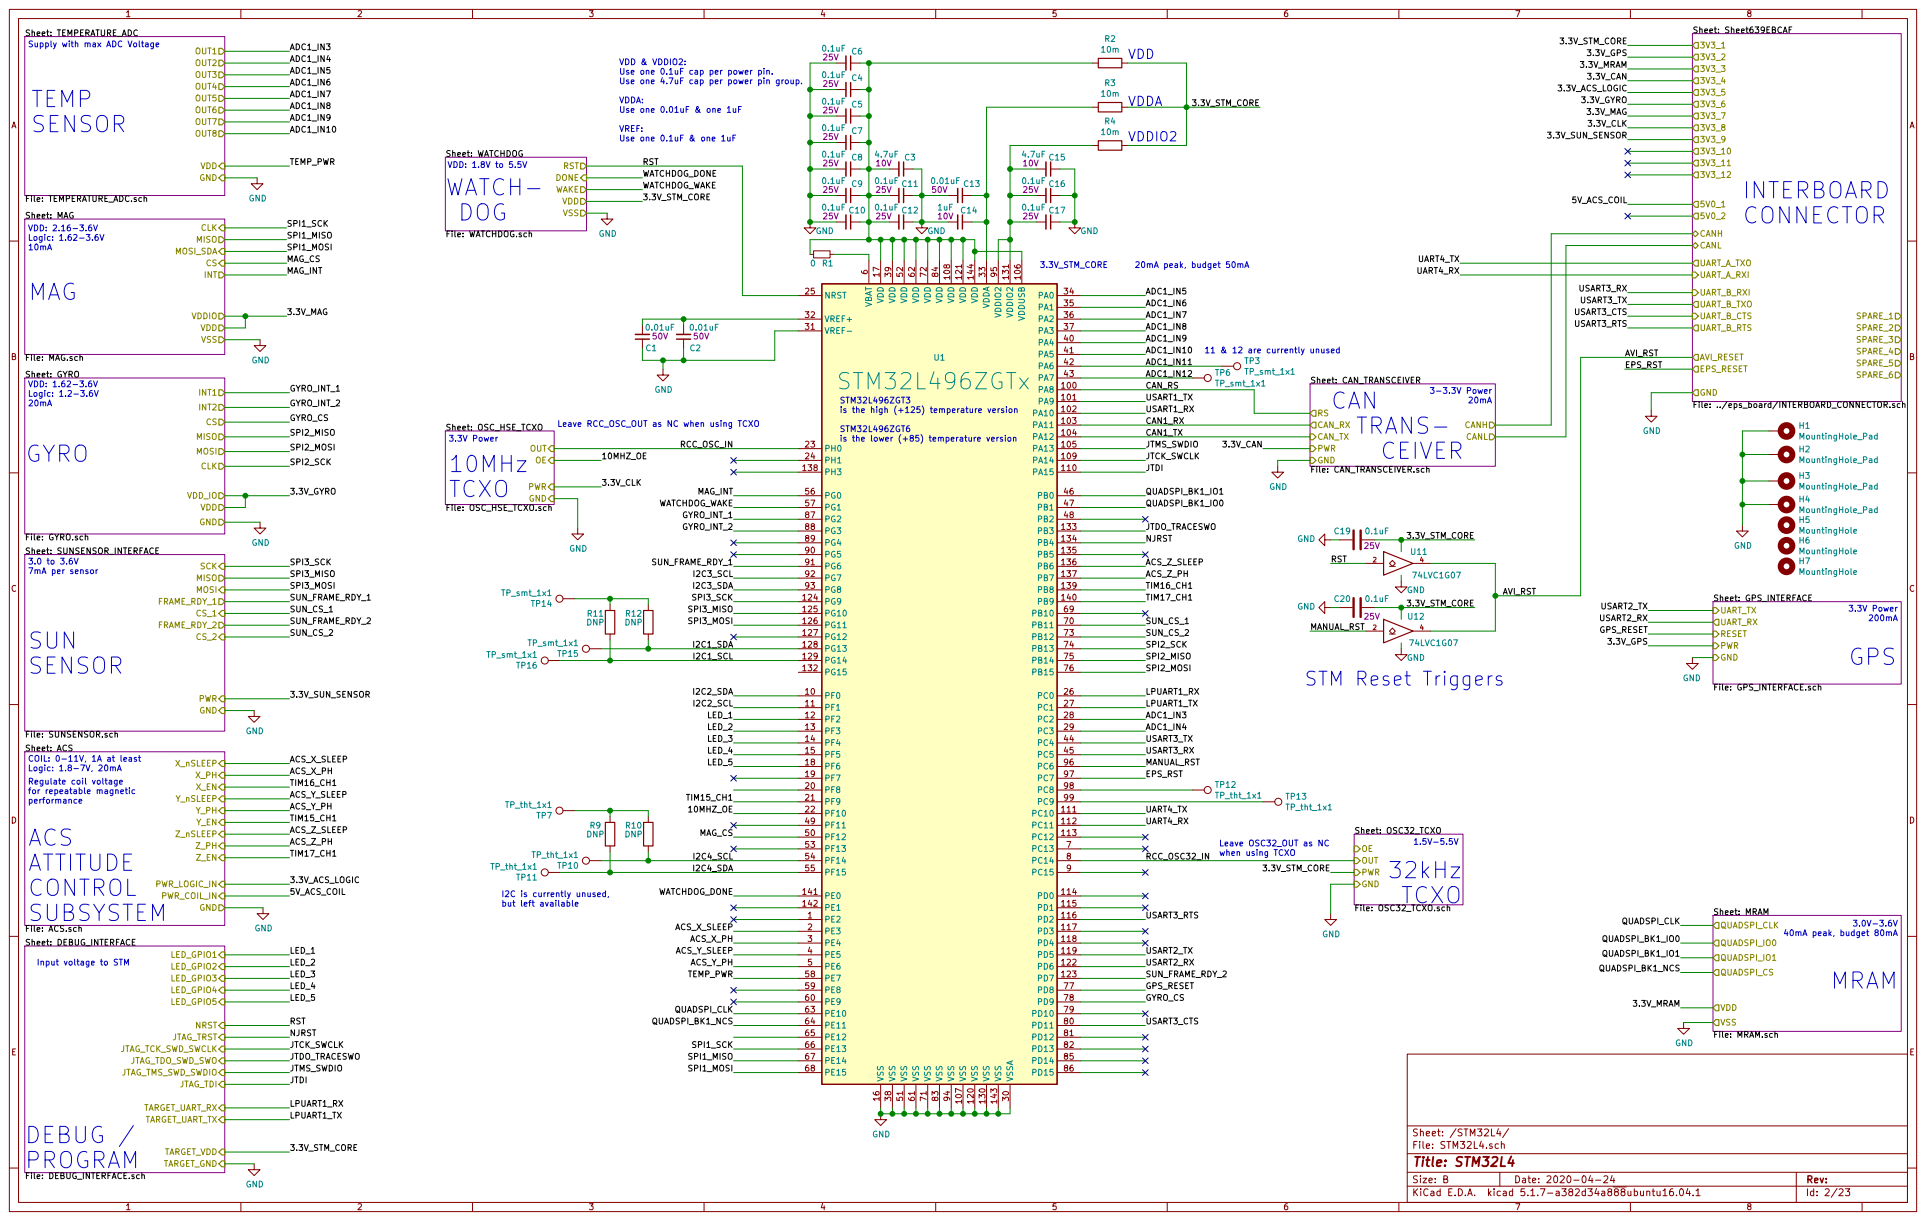
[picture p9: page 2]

VDD & VDDIO2: Use one 0.1uF cap per power pin.

Use one 4.7uF cap per power pin group. VDDA: Use one 0.01uF & one 1uF VREF: Use one 0.1uF & one 1uF

VSS RST DONE WAKE

6 VDD 108 VDD 121 VDD 144 VDD 17 VDD 39 VDD 52 VDD 62 VDD 72 VDD 84 VDDA 33 VDDIO2 131 VDDIO2 95 VDDUSB 106 VREF+ 32 VREF- 31 VSS 107 VSS 120 VSS 130 VSS 143 VSS 16 VSS 38 VSS 51 VSS 61 VSS 71 VSS 83 VSS 94 VSSA 30 U1 STM32L496ZGTx

STM32L496ZGT3
is the high (+125) temperature version STM32L496ZGT6

Leave RCC_OSC_OUT as NC when using TCXO

is the lower (+85) temperature version

File: CAN_TRANSCEIVER.sch PWR GND

File: GPS_INTERFACE.sch PWR GND

Leave OSC32_OUT as NC when using TCXO

File: OSC32_TCXO.sch PWR GND OEOUT
32kHz
TCXO

I2C is currently unused, but left available

Input voltage to STM

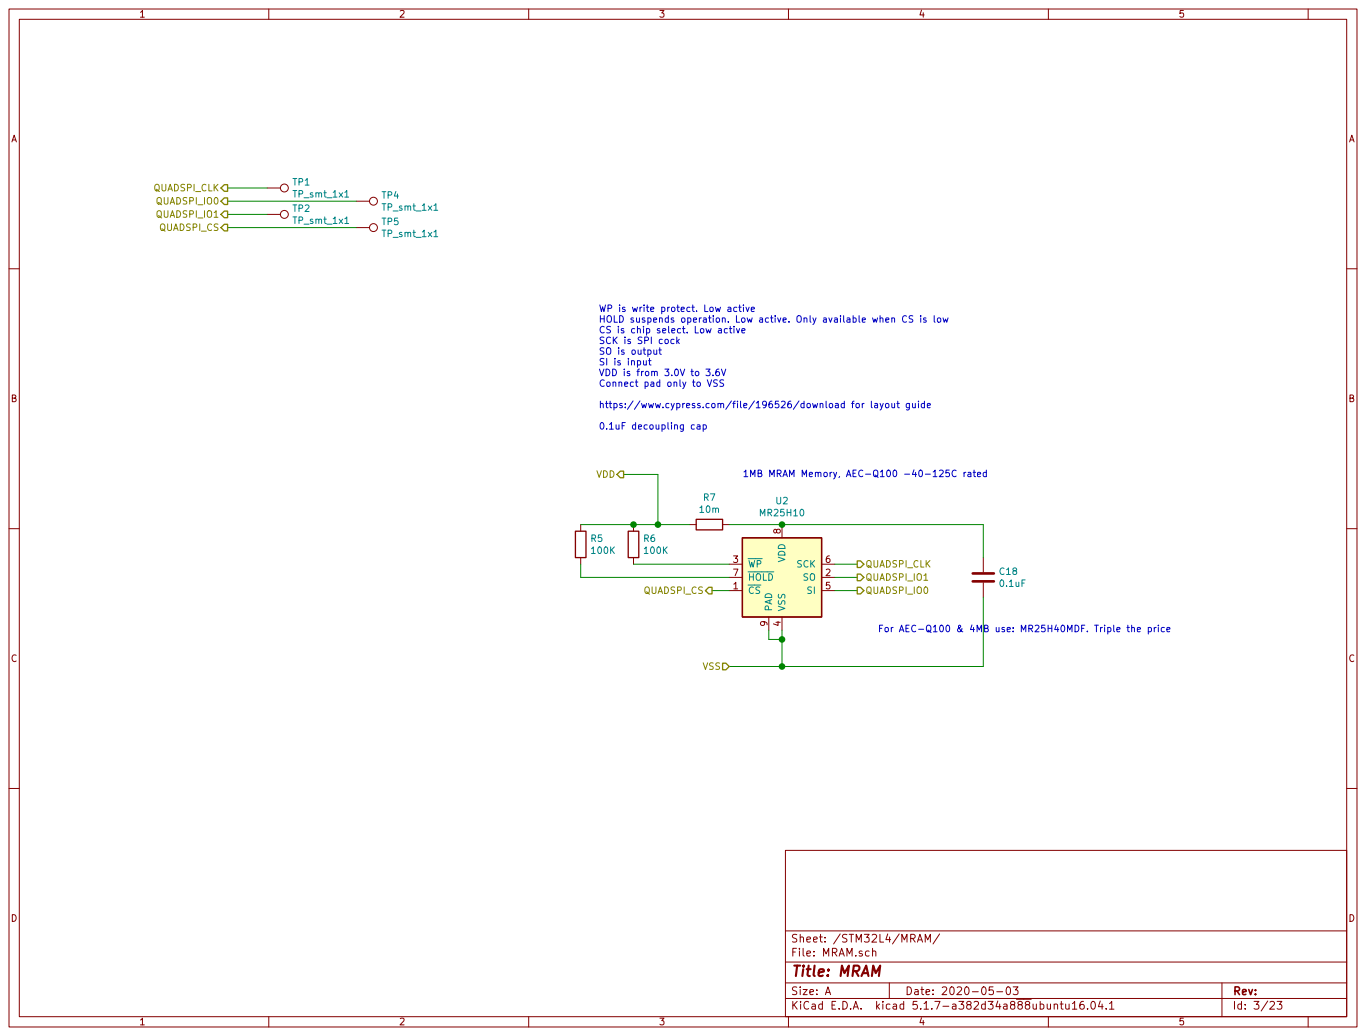
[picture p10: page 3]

WP is write protect. Low active
HOLD suspends operation. Low active. Only available when CS is low
CS is chip select. Low active SCK is SPI cock SO is output

SI is input VDD is from 3.0V to 3.6V Connect pad only to VSS

https://www.cypress.com/file/196526/download for layout guide

1MB MRAM Memory, AEC-Q100 -40-125C rated

4 SI 5 SCK 6 HOLD 7 VDD

For AEC-Q100 & 4MB use: MR25H40MDF. Triple the price

File: MRAM.sch Sheet: /STM32L4/MRAM/
Id: 3/23 Title: MRAM

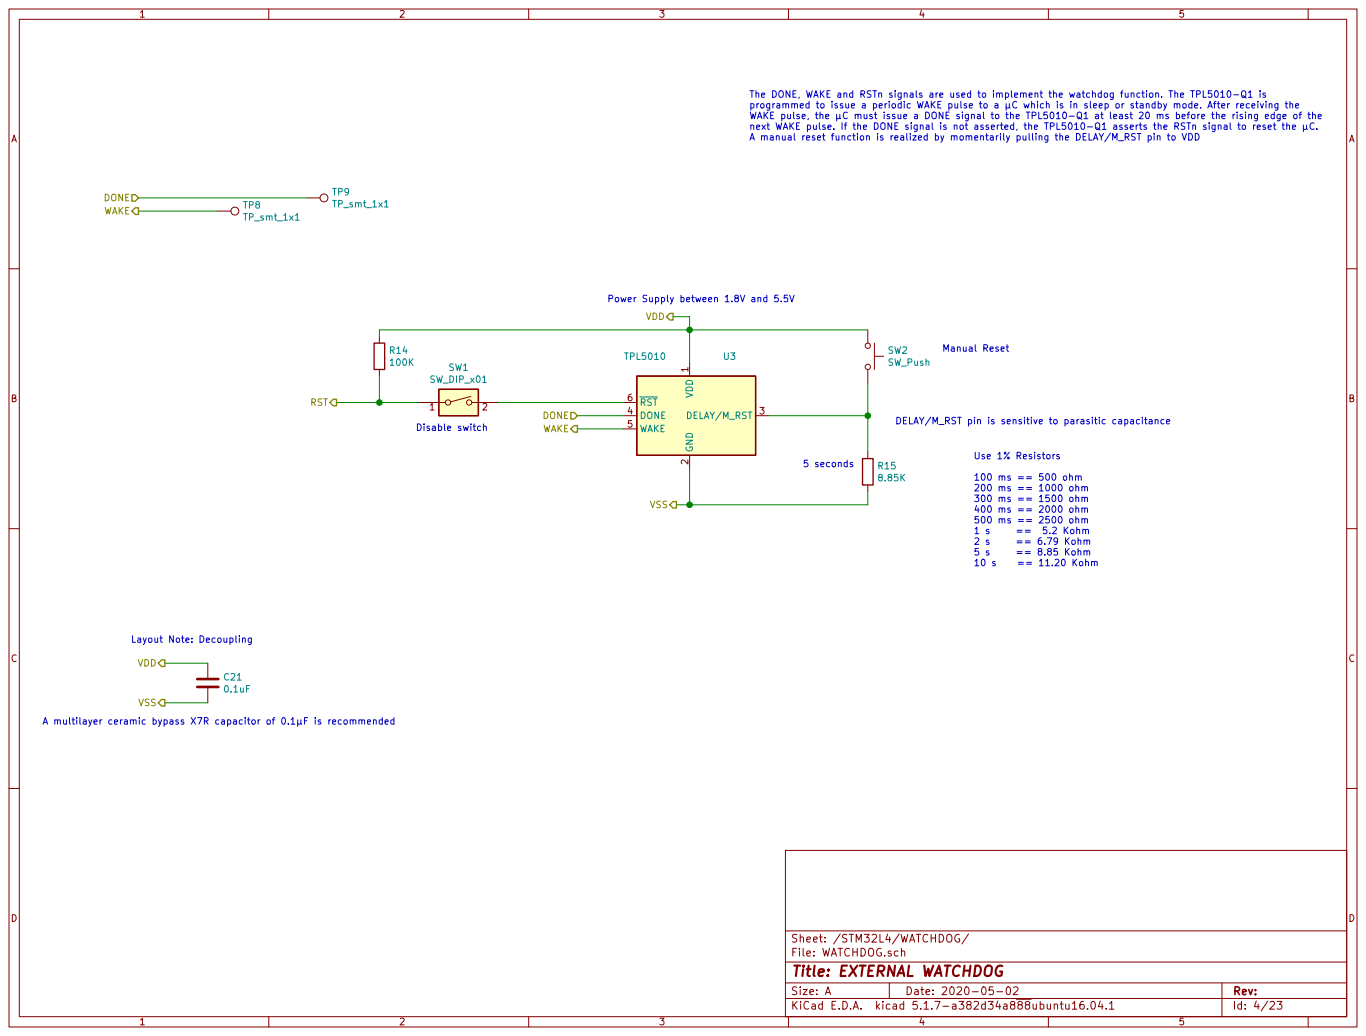
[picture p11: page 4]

5 seconds The DONE, WAKE and RSTn signals are used to implement the watchdog function. The TPL5010-Q1 is
programmed to issue a periodic WAKE pulse to a C which is in sleep or standby mode. After receiving the
WAKE pulse, the C must issue a DONE signal to the TPL5010-Q1 at least 20 ms before the rising edge of the
next WAKE pulse. If the DONE signal is not asserted, the TPL5010-Q1 asserts the RSTn signal to reset the C.
A manual reset function is realized by momentarily pulling the DELAY/M_RST pin to VDD

2 DELAY/M_RST 3 DONE 4 WAKE 5 RST 6TPL5010 U3 R14

DELAY/M_RST pin is sensitive to parasitic capacitance Use 1% Resistors 100 ms == 500 ohm

A multilayer ceramic bypass X7R capacitor of 0.1F is recommended

File: WATCHDOG.sch Sheet: /STM32L4/WATCHDOG/
Id: 4/23 Title: EXTERNAL WATCHDOG

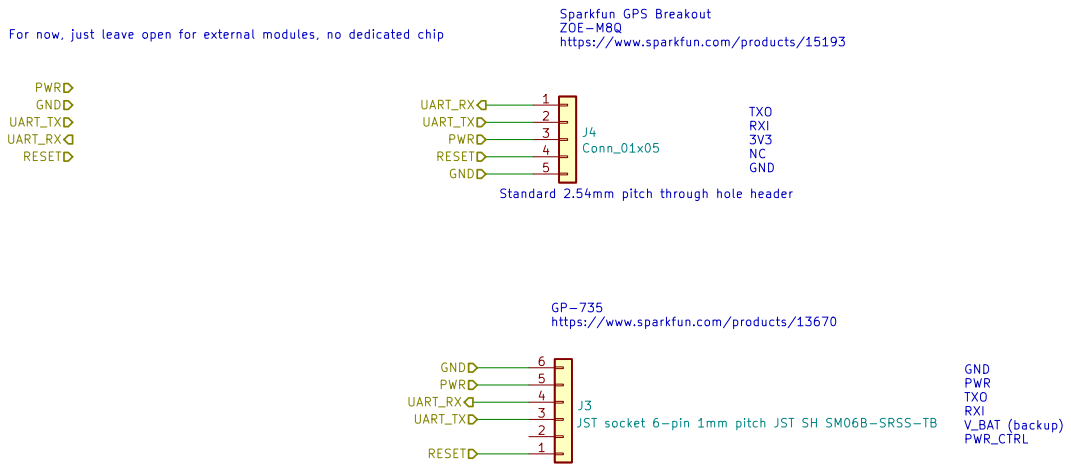
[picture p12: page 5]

Sparkfun GPS Breakout ZOE-M8Q

https://www.sparkfun.com/products/15193

Standard 2.54mm pitch through hole header GP-735

https://www.sparkfun.com/products/13670

Sheet: /STM32L4/GPS_INTERFACE/
File: GPS_INTERFACE.sch
Id: 5/23 Title: GPS interface

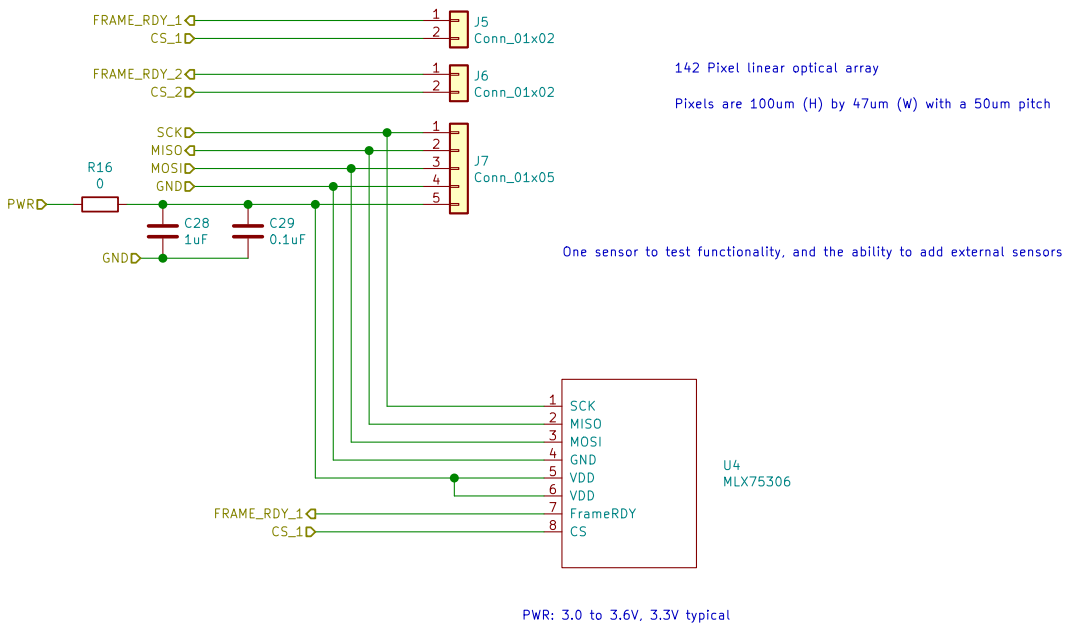
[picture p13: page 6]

142 Pixel linear optical array

Pixels are 100um (H) by 47um (W) with a 50um pitch

File: SUNSENSOR.sch Sheet: /STM32L4/SUNSENSOR_INTERFACE/
Id: 6/23 Title: Sun Sensor Interface

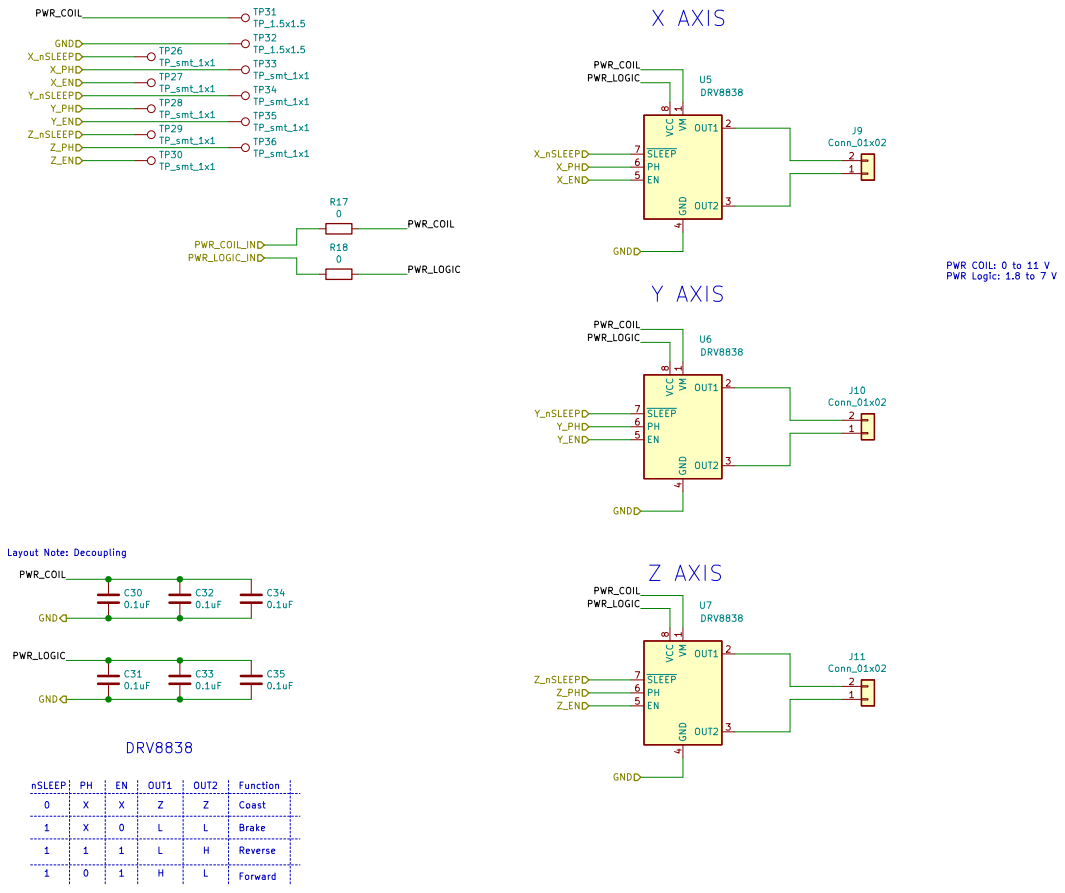
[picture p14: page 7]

File: ACS.sch Sheet: /STM32L4/ACS/
Id: 7/23 Title: Attitude Control System


DEBUG LED
Target's RX and TX pinsVf=2.0V

The TDI and TDO pins here match with the target's (the STM32's) TDI and TDO pins.

SRST = System Reset
TRST = JTAG specific reset

The series resistors are useful on high-speed traces.
https://electronics.stackexchange.com/questions/7709/why-put-a-resistor-in-series-with-signal-line

So I'm going with 50 ohm

SWO (Serial Wire output) optional JTAG
TDI (Test Data In)
TDO (Test Data Out)
TCK (Test Clock)
TMS (Test Mode Select)
TRST (Test Reset) optional.

SWCLK (Clock signal to target CPU)
SWDIO (Bi-directional data pin)

Sheet: /STM32L4/DEBUG_INTERFACE/
File: DEBUG_INTERFACE.sch
Id: 8/23 Title: DEBUG INTERFACE


By default, OE is tied high so the chip is enabled immediatly



Low ESR cap, close proximity to the chip VDD 2.16V to 3.6V

File: MAG.sch Sheet: /STM32L4/MAG/
Id: 11/23 Title: Magnetic Sensor MMC5983MA


VOUT Sheet: sheet5EC02641 File: NTC_THERMISTOR.sch VSS

VOUT Sheet: sheet5EC02640 File: NTC_THERMISTOR.sch VSS

Sheet: /STM32L4/TEMPERATURE_ADC/
File: TEMPERATURE_ADC.sch
Id: 12/23 Title: Temperature Sensors


Max linearity around temperature X when Rbias==Rt @ temperature X.

This circuit ranges from 46k ohm impedance (NTC high resist, cold)
to 1k ohm impedance (NTC low resist)

T2 = second temp point in Kelvin R1 = thermistor's resistance at T1 in Ohms R2 = thermistor's resistance at T2 in Ohms B (T1/ T2) = ((T2 x T1) / (T2 - T1)) x ln(R1/R2)
T1 = first temp point in Kelvin

https://www.electro-tech-online.com/tools/thermistor-resistance-calculator.php
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

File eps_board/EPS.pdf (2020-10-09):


Sheet: sheet5F71F776 File: IDEAL_DIODE.sch VIN1 VIN2 GND

VOUT BAT VNTC GND

File: BATTERY.sch VBAT GND
VNTC
NTC
Battery 1,2

Power Management IC (PMIC)

VOUT2

Battery 3,4

5V0_2 AVI_RESET Sheet: sheet5F62C2E5 File: LTC3130.sch VIN GND

Id: 1/35 Title: Current Monitor File: EPS.sch Sheet: /

Sheet: /SOLAR_INPUT/
File: SOLAR_INPUT.sch
Id: 2/35 Title: Solar Input


a schottky is used becuase It's simpler than a MOSFET VMAX = 5.5V for IN, OUT, BAT

pullup HPWR with VOUT.
HPWR will always be high
assuming device enabled

the BAT pin (i.e., ideal diode). EXT must be at
least 4.5V to trip WALL

ACPR
POL: Battery Current Status Polarity Pin.
This open-drain output pin indicates whether the current
flowing out of the ISTAT pin represents one-thousandth
of the cur-rent flowing into or out of the BAT pins.
The POL pin will pull down when current is fl owing
out of the BAT pin (i.e., charging) and will assume a
high impedance state when current is flowing into

Indicates wall adapter present. Disabled if IN==OUT==BAT==0V or shutdown CHRG: Open-Drain Charge Status Output.
When the battery is beingcharged, the CHRG pin
is pulled low by an internal N-channel MOSFET.
When the timer runs out or the charge current
drops below a programmable current level
or the input supply or output supply is removed,
the CHRG pin is forced to a high impedance state.

ACPR: Wall Adapter present. Active Low open drain.


Bypass CAP for MCP VIN

One heater per battery. 150mA current Limit set by 3090 Ohm resistor

Bypass CAP for FPF VIN

Bypass CAP for FPF VOUT

File: BATTERY.sch Sheet: /BATTERY/ TH? Thermistor_NTC

https://www.keyelco.com/product.cfm/product_id/826
Battery holder ^^^

NTC is placed on only 1 battery.
It is assumed that one battery's temperature
will closely follow the others.

NTC output for battery charger
and heater circuit (see above)

Id: 4/35 Title: Battery, Battery Heater, NTC


File: SOLAR_INPUT.sch Sheet: /sheet5F3BB619/
Id: 5/35 Title: Solar Input

File: SOLAR_INPUT.sch Sheet: /sheet5F3BC7D0/
Id: 6/35 Title: Solar Input

File: SOLAR_INPUT.sch Sheet: /sheet5F3BD955/
Id: 7/35 Title: Solar Input

File: SOLAR_INPUT.sch Sheet: /sheet5F3BED7E/
Id: 8/35 Title: Solar Input

File: SOLAR_INPUT.sch Sheet: /sheet5F3C01BD/
Id: 9/35 Title: Solar Input

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

pullup HPWR with VOUT.
HPWR will always be high
assuming device enabled

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

ACPR: Wall Adapter present. Active Low open drain.


Bypass CAP for MCP VIN

One heater per battery. 150mA current Limit set by 3090 Ohm resistor

Bypass CAP for FPF VIN

Bypass CAP for FPF VOUT

File: BATTERY.sch Sheet: /sheet5F4CFCDF/ TH? Thermistor_NTC

https://www.keyelco.com/product.cfm/product_id/826
Battery holder ^^^

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

NTC output for battery charger
and heater circuit (see above)

Id: 11/35 Title: Battery, Battery Heater, NTC


STAT2 STAT1 VOUT2 VOUT1 Weekly pulldown EN2, so EN2 is always enabled

Weekly pullup EN1, so EN1 is always enabled

0.5A current limit is set

Voltage Threasholds for the Enable pins:
Venth = 0.8V with Venhyst = 0.055V


PGOOD is open drain.
Pulled low when VOUT is less than 7.5% programmed value
High-Z when VOUT is within 5% programmed value

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

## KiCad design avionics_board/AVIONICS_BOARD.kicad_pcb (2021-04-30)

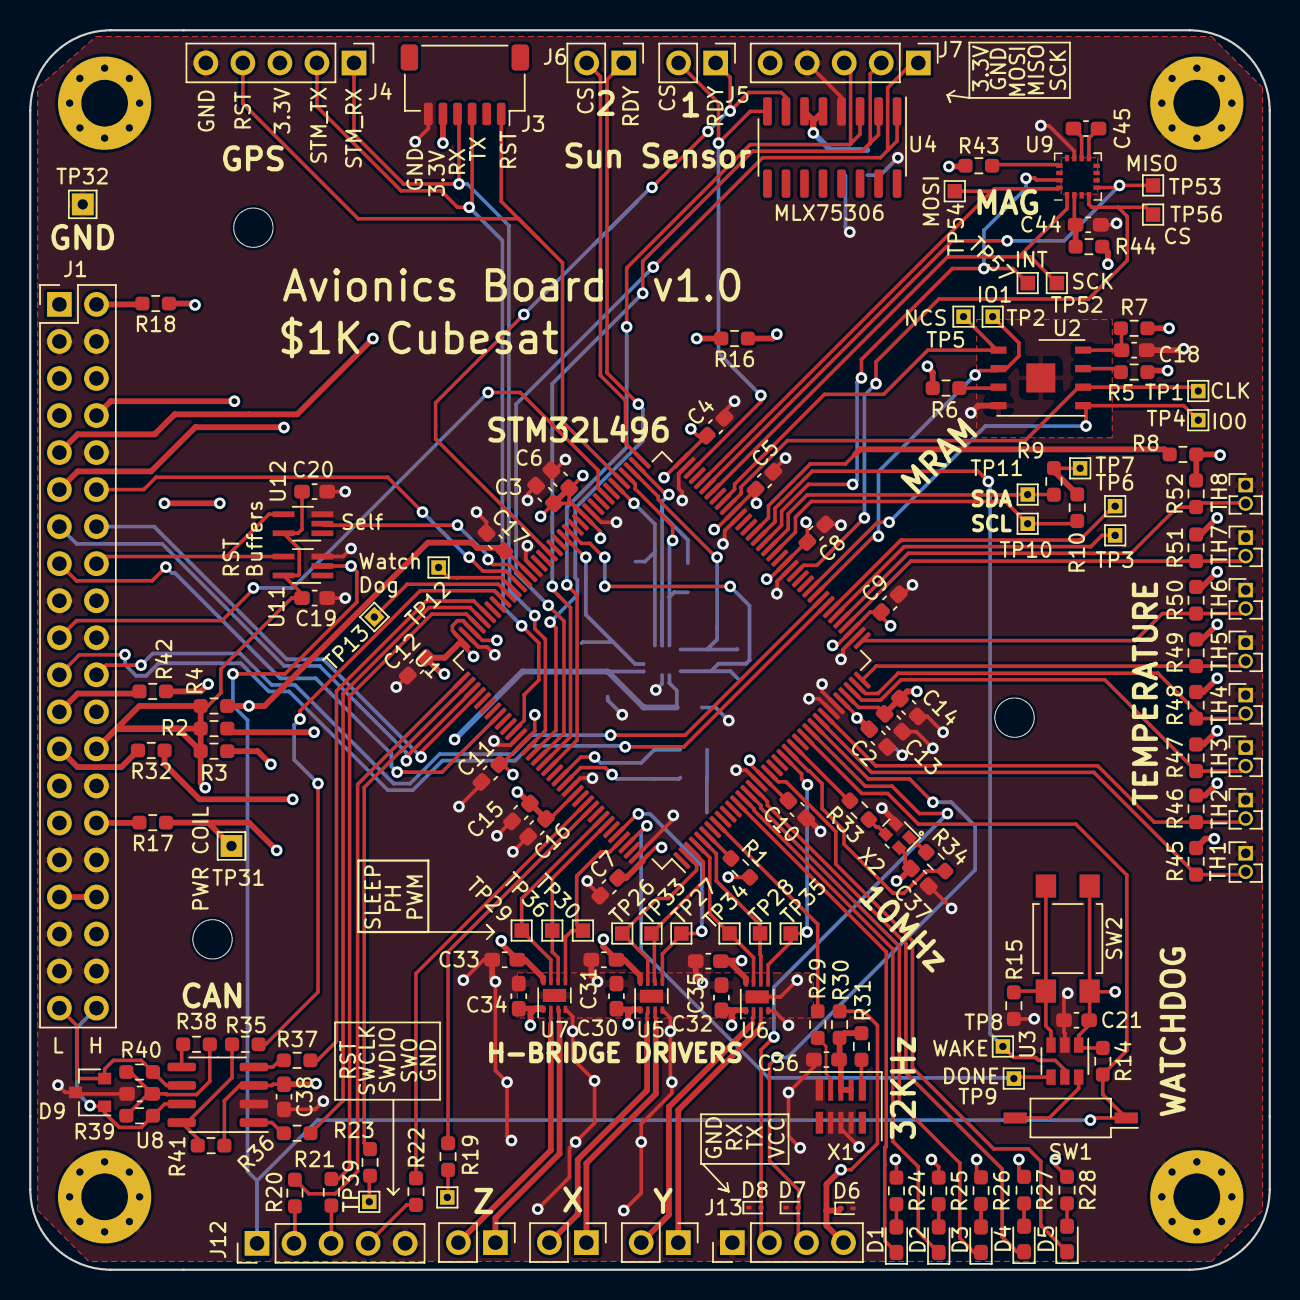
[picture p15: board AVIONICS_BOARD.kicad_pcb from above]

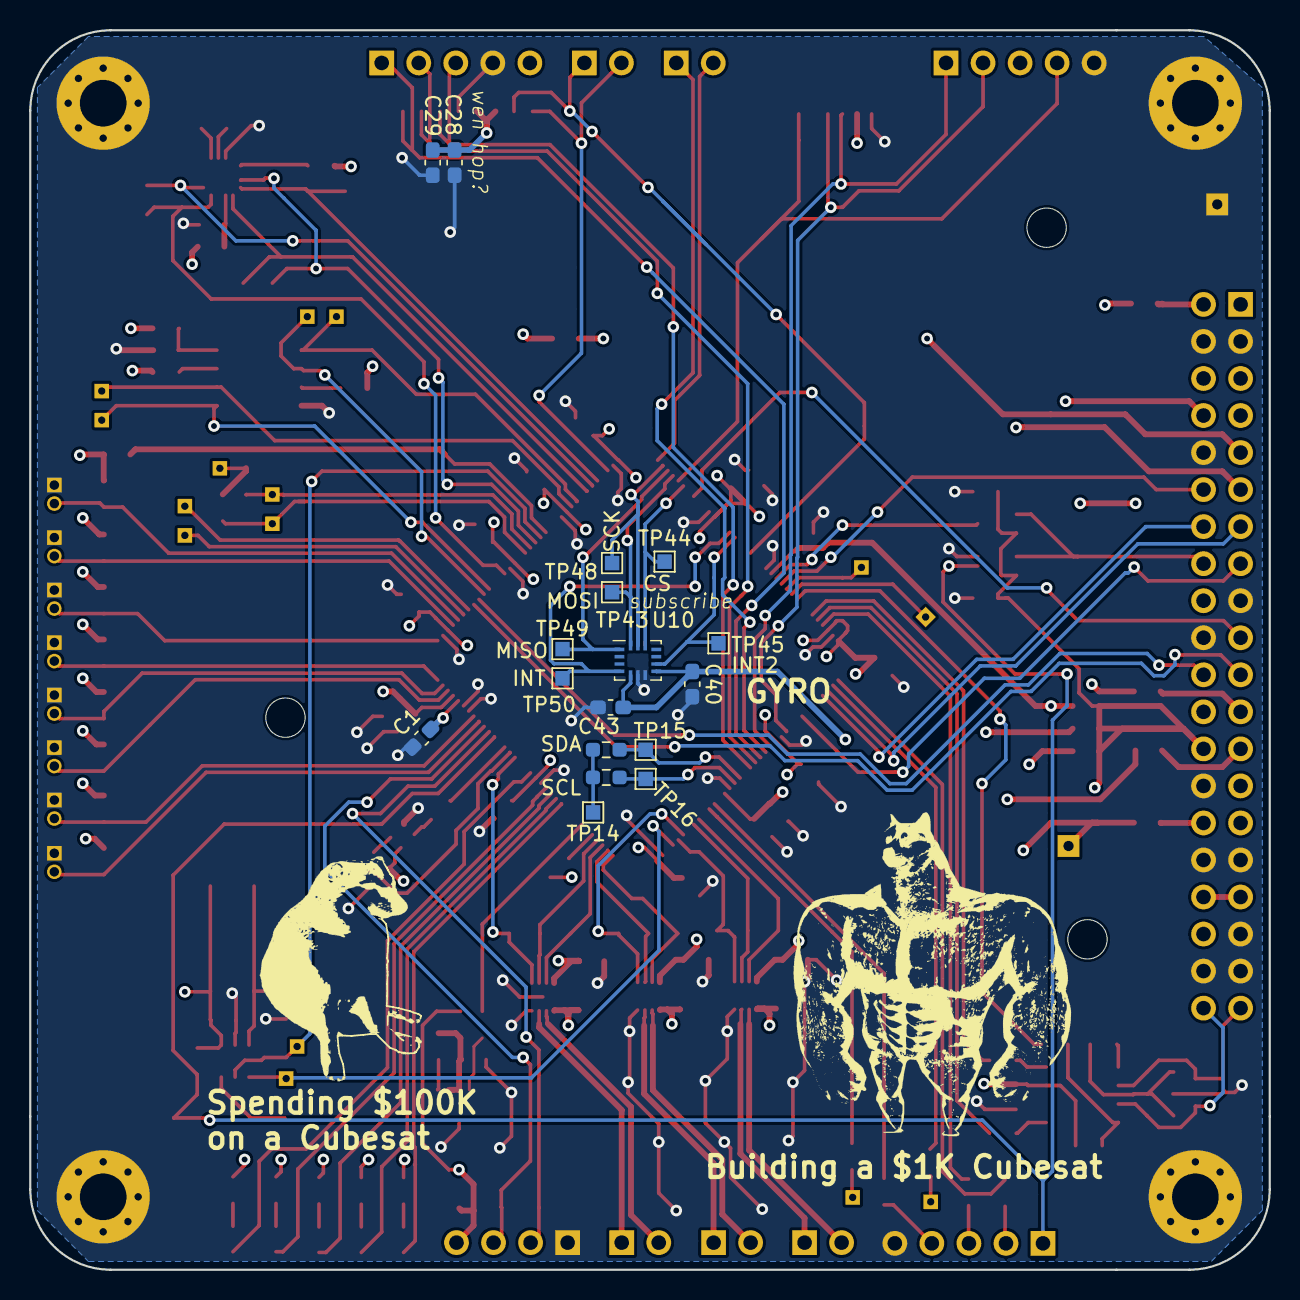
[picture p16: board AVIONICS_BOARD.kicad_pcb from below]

Board: 4 copper layers, 85.0 x 85.0 mm, 179 parts (17 on the bottom side), 143 nets.

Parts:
C1, C2, C13: 0.01uF; C_0603_1608Metric_Pad1.08x0.95mm_HandSolder
C3, C15: 4.7uF; C_0603_1608Metric_Pad1.08x0.95mm_HandSolder
C4, C5, C6, C7, C8, C9, C10, C11, C12, C16, C17, C18, C19, C20, C21, C29, C30, C31, C32, C33, C34, C35, C36, C37, C38, C40, C43: 0.1uF; C_0603_1608Metric_Pad1.08x0.95mm_HandSolder
C14, C28, C44: 1uF; C_0603_1608Metric_Pad1.08x0.95mm_HandSolder
C39: 4.7nF; C_0603_1608Metric_Pad1.08x0.95mm_HandSolder
C45: 10uF; C_0603_1608Metric_Pad1.08x0.95mm_HandSolder
D1: LED_SMD_RED; LED_0603_1608Metric_Pad1.05x0.95mm_HandSolder
D2: LED_SMD_GREEN; LED_0603_1608Metric_Pad1.05x0.95mm_HandSolder
D3, D4, D5: LED_SMD_YELLOW; LED_0603_1608Metric_Pad1.05x0.95mm_HandSolder
D6, D7, D8: ESD9B5.0ST5G; D_SOD-923
D9: NUP2105L; SOT-23
H1, H2, H3, H4: MountingHole_Pad; MountingHole_3.2mm_M3_Pad_Via
H5, H6, H7: MountingHole; MountingHole_2.7mm
J1: Conn_02x20_Odd_Even; PinHeader_2x20_P2.54mm_Vertical
J3: JST socket 6-pin 1mm pitch JST SH SM06B-SRSS-TB; JST_SH_SM06B-SRSS-TB_1x06-1MP_P1.00mm_Horizontal
J4, J7, J12: Conn_01x05; PinHeader_1x05_P2.54mm_Vertical
J5, J6, J9, J10, J11: Conn_01x02; PinHeader_1x02_P2.54mm_Vertical
J13: Conn_01x04_Male; PinHeader_1x04_P2.54mm_Vertical
R1, R8, R16, R17, R18, R29, R30, R31, R32, R33, R34, R35, R36, R37, R38, R42, R43, R44: 0; R_0603_1608Metric_Pad0.98x0.95mm_HandSolder
R2, R3, R4, R7: 10m; R_0603_1608Metric_Pad0.98x0.95mm_HandSolder
R5, R6, R14, R41: 100K; R_0603_1608Metric_Pad0.98x0.95mm_HandSolder
R9, R10, R11, R12: DNP; R_0603_1608Metric_Pad0.98x0.95mm_HandSolder
R15: 8.85K; R_0603_1608Metric_Pad0.98x0.95mm_HandSolder
R19, R20, R21, R22, R23: 49.9; R_0603_1608Metric_Pad0.98x0.95mm_HandSolder
R24, R25, R26, R27, R28: 330; R_0603_1608Metric_Pad0.98x0.95mm_HandSolder
R39, R40: 60.4; R_0603_1608Metric_Pad0.98x0.95mm_HandSolder
R45, R46, R47, R48, R49, R50, R51, R52: 47K; R_0603_1608Metric_Pad0.98x0.95mm_HandSolder
SW1: SW_DIP_x01; SW_DIP_SPSTx01_Slide_Copal_CHS-01B_W7.62mm_P1.27mm
SW2: SW_Push; SW_SPST_TL3305A
TH1, TH2, TH3, TH4, TH5, TH6, TH7, TH8: Thermistor_NTC; PinHeader_1x02_P1.27mm_Vertical
TP1, TP2, TP3, TP4, TP5, TP6, TP8, TP9: TP_smt_1x1; TestPoint_THTPad_1.0x1.0mm_Drill0.5mm
TP7, TP10, TP11, TP12, TP13: TP_tht_1x1; TestPoint_THTPad_1.0x1.0mm_Drill0.5mm
TP14, TP15, TP16, TP26, TP27, TP28, TP29, TP30, TP33, TP34, TP35, TP36, TP43, TP44, TP45, TP48, TP49, TP50, TP52, TP53, TP54, TP56, TP57: TP_smt_1x1; TestPoint_Pad_1.0x1.0mm
TP31, TP32: TP_1.5x1.5; TestPoint_THTPad_1.5x1.5mm_Drill0.7mm
TP37, TP39: TP_1.5x1.5; TestPoint_THTPad_1.0x1.0mm_Drill0.5mm
U1: STM32L496ZGTx; LQFP-144_20x20mm_P0.5mm
U2: MR25H10; DFN-8-1EP_6x5mm_P1.27mm_EP2x2mm
U3: TPL5010; SOT-23-6
U4: MLX75306; SOIC-16_3.9x9.9mm_P1.27mm
U5, U6, U7: DRV8838; WSON-8-1EP_2x2mm_P0.5mm_EP0.9x1.6mm
U8: SN65HVD230; SOIC-8_3.9x4.9mm_P1.27mm
U9: MMC5983MA; LGA-16_3x3mm_P0.5mm
U10: BMG250; Bosch_LGA-14_3x2.5mm_P0.5mm
U11, U12: 74LVC1G07; SOT-353_SC-70-5_Handsoldering
X1: TG-3541CE; Oscillator_SMD_SeikoEpson_TG3541CE-10Pin_3.2x2.5mm_HandSold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
X2: ECS-TXO-2016; Oscillator_SMD_ECS_TXO-2016-xx-xxx-4Pin_2.0x1.6mm

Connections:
/STM32L4/3.3V_ACS_LOGIC: J1.2, R18.2
/STM32L4/3.3V_CAN: C38.1, J1.5, R41.1, U8.3
/STM32L4/3.3V_CLK: J1.25, R32.2
/STM32L4/3.3V_GPS: J1.24, J3.5, J4.3
/STM32L4/3.3V_GYRO: J1.23, R42.2
/STM32L4/3.3V_MAG: J1.8, R43.2, R44.2
/STM32L4/3.3V_MRAM: J1.11, R5.1, R6.1, R7.2
/STM32L4/3.3V_SUN_SENSOR: J1.9, R16.2
/STM32L4/5V_ACS_COIL: J1.30, R17.2
/STM32L4/10MHZ_OE: R34.2, U1.22
/STM32L4/ACS/PWR_COIL: C30.1, C32.1, C34.1, R17.1, TP31.1, U5.1, U6.1, U7.1
/STM32L4/ACS/PWR_LOGIC: C31.1, C33.1, C35.1, R18.1, U5.8, U6.8, U7.8
/STM32L4/ACS_X_PH: TP33.1, U1.3, U5.6
/STM32L4/ACS_X_SLEEP: TP26.1, U1.2, U5.7
/STM32L4/ACS_Y_PH: TP28.1, U1.5, U6.6
/STM32L4/ACS_Y_SLEEP: TP34.1, U1.4, U6.7
/STM32L4/ACS_Z_PH: TP36.1, U1.137, U7.6
/STM32L4/ACS_Z_SLEEP: TP29.1, U1.136, U7.7
/STM32L4/ADC1_IN3: R45.1, TH1.2, U1.28
/STM32L4/ADC1_IN4: R46.1, TH2.2, U1.29
/STM32L4/ADC1_IN5: R47.1, TH3.2, U1.34
/STM32L4/ADC1_IN6: R48.1, TH4.2, U1.35
/STM32L4/ADC1_IN7: R49.1, TH5.2, U1.36
/STM32L4/ADC1_IN8: R50.1, TH6.2, U1.37
/STM32L4/ADC1_IN9: R51.1, TH7.2, U1.40
/STM32L4/ADC1_IN10: R52.1, TH8.2, U1.41
/STM32L4/ADC1_IN11: TP3.1, U1.42
/STM32L4/ADC1_IN12: TP6.1, U1.43
/STM32L4/AVI_RST: J1.16, U11.4, U12.4
/STM32L4/CAN1_RX: R37.2, U1.103
/STM32L4/CAN1_TX: R36.2, U1.104
/STM32L4/CAN_RS: R35.2, U1.100
/STM32L4/CAN_TRANSCEIVER/CANH: D9.1, J1.40, R39.1, U8.7
/STM32L4/CAN_TRANSCEIVER/CANL: D9.2, J1.39, R40.2, U8.6
/STM32L4/CAN_TRANSCEIVER/Vref: R38.2, U8.5
/STM32L4/EPS_RST: J1.12, U1.97
/STM32L4/GPS_RESET: J3.1, J4.4, U1.77
/STM32L4/GYRO_CS: TP44.1, U1.78, U10.12
/STM32L4/GYRO_INT_1: TP50.1, U1.87, U10.4
/STM32L4/GYRO_INT_2: TP45.1, U1.88, U10.9
/STM32L4/I2C1_SCL: R11.2, TP16.1, U1.129
/STM32L4/I2C1_SDA: R12.2, TP15.1, U1.128
/STM32L4/I2C4_SCL: R10.2, TP10.1, U1.54
/STM32L4/I2C4_SDA: R9.2, TP11.1, U1.55
/STM32L4/JTCK_SWCLK: R20.1, U1.109
/STM32L4/JTDI: R23.1, U1.110
/STM32L4/JTDO_TRACESWO: R22.1, U1.133
/STM32L4/JTMS_SWDIO: R21.1, U1.105
/STM32L4/LED_1: D1.1, U1.12
/STM32L4/LED_2: D2.1, U1.13
/STM32L4/LED_3: D3.1, U1.14
/STM32L4/LED_4: D4.1, U1.15
/STM32L4/LED_5: D5.1, U1.18
/STM32L4/LPUART1_RX: D8.2, J13.2, U1.26
/STM32L4/LPUART1_TX: D7.2, J13.3, U1.27
/STM32L4/MAG_CS: TP56.1, U1.50, U9.4
/STM32L4/MAG_INT: TP57.1, U1.56, U9.15
/STM32L4/MANUAL_RST: U1.96, U12.2
/STM32L4/NJRST: R19.1, U1.134
/STM32L4/OSC32_TCXO/OE: R31.1, X1.1
/STM32L4/QUADSPI_BK1_IO0: TP4.1, U1.47, U2.5
/STM32L4/QUADSPI_BK1_IO1: TP2.1, U1.46, U2.2
/STM32L4/QUADSPI_BK1_NCS: TP5.1, U1.64, U2.1
/STM32L4/QUADSPI_CLK: TP1.1, U1.63, U2.6
/STM32L4/RCC_OSC32_IN: R29.2, U1.8
/STM32L4/RCC_OSC_IN: R33.2, U1.23
/STM32L4/RST: J12.1, R14.2, SW1.1, U1.25, U11.2
/STM32L4/SPI1_MISO: TP53.1, U1.67, U9.5
/STM32L4/SPI1_MOSI: TP54.1, U1.68, U9.16
/STM32L4/SPI1_SCK: TP52.1, U1.66, U9.1
/STM32L4/SPI2_MISO: TP49.1, U1.75, U10.1
/STM32L4/SPI2_MOSI: TP43.1, U1.76, U10.14
/STM32L4/SPI2_SCK: TP48.1, U1.74, U10.13
/STM32L4/SPI3_MISO: J7.2, U1.125, U4.2
/STM32L4/SPI3_MOSI: J7.3, U1.126, U4.3
/STM32L4/SPI3_SCK: J7.1, U1.124, U4.1
/STM32L4/SUN_CS_1: J5.2, U1.70, U4.8
/STM32L4/SUN_CS_2: J6.2, U1.73
/STM32L4/SUN_FRAME_RDY_1: J5.1, U1.91, U4.7
/STM32L4/SUN_FRAME_RDY_2: J6.1, U1.123
/STM32L4/Sheet639EBCAF/5V0_2: J1.33, J1.34
/STM32L4/TEMPERATURE_ADC/INTRNL_VDD: R8.1, R45.2, R46.2, R47.2, R48.2, R49.2, R50.2, R51.2, R52.2
/STM32L4/TEMP_PWR: R8.2, U1.58
/STM32L4/TIM15_CH1: TP35.1, U1.21, U6.5
/STM32L4/TIM16_CH1: TP27.1, U1.139, U5.5
/STM32L4/TIM17_CH1: TP30.1, U1.140, U7.5
/STM32L4/UART4_RX: J1.14, U1.112
/STM32L4/UART4_TX: J1.13, U1.111
/STM32L4/USART2_RX: J3.4, J4.1, U1.122
/STM32L4/USART2_TX: J3.3, J4.2, U1.119
/STM32L4/USART3_CTS: J1.19, U1.80
/STM32L4/USART3_RTS: J1.15, U1.116
/STM32L4/USART3_RX: J1.22, U1.45
/STM32L4/USART3_TX: J1.21, U1.44
/STM32L4/WATCHDOG_DONE: TP9.1, U1.141, U3.4
/STM32L4/WATCHDOG_WAKE: TP8.1, U1.57, U3.5
GND: C1.1, C2.1, C3.1, C4.2, C5.2, C6.2, C7.2, C8.2, C9.2, C10.2, C11.1, C12.1, C13.2, C14.2, C15.1, C16.1, C17.1, C18.2, C19.1, C20.1, C21.2, C28.2, C29.2, C30.2, C31.2, C32.2, C33.2, C34.2, C35.2, C36.2, C37.2, C38.2, C39.2, C40.2, C43.2, C44.2, D6.2, D7.1, D8.1, D9.3, H1.1, H2.1, H3.1, H4.1, J1.3, J1.4, J1.10, J1.17, J1.20, J1.28, J1.31, J1.32, J1.35, J1.37, J1.38, J3.6, J4.5, J7.4, J12.5, J13.1, R15.2, TH1.1, TH2.1, TH3.1, TH4.1, TH5.1, TH6.1, TH7.1, TH8.1, TP32.1, U1.16, U1.30, U1.31, U1.38, U1.51, U1.61, U1.71, U1.83, U1.94, U1.107, U1.120, U1.130, U1.143, U2.4, U2.9, U3.2, U4.4, U5.4, U5.9, U6.4, U6.9, U7.4, U7.9, U8.2, U9.11, U10.6, U10.7, U11.3, U12.3, X1.5, X1.7, X1.8, X1.9, X2.2
unnamed: C1.2, C2.2, U1.32
unnamed: C3.2, C4.1, C5.1, C6.1, C7.1, C8.1, C9.1, C10.1, C11.2, C12.2, R1.2, R2.2, U1.17, U1.39, U1.52, U1.62, U1.72, U1.84, U1.106, U1.108, U1.121, U1.144
unnamed: C13.1, C14.1, R3.2, U1.33
unnamed: C15.2, C16.2, C17.2, R4.2, U1.95, U1.131
unnamed: C18.1, R7.1, U2.8
unnamed: C28.1, C29.1, J7.5, R16.1, U4.5, U4.6
unnamed: C36.1, R30.1, R31.2, X1.2, X1.3
unnamed: C37.1, R32.1, X2.4
unnamed: C39.1, R38.1, R39.2, R40.1
unnamed: C40.1, C43.1, R42.1, U10.5, U10.8
unnamed: C44.1, R44.1, U9.2
unnamed: C45.1, U9.9
unnamed: C45.2, U9.10
unnamed: D1.2, R24.2
unnamed: D2.2, R25.2
unnamed: D3.2, R26.2
unnamed: D4.2, R27.2
unnamed: D5.2, R28.2
unnamed: J9.1, U5.3
unnamed: J9.2, U5.2
unnamed: J10.1, U6.3
unnamed: J10.2, U6.2
unnamed: J11.1, U7.3
unnamed: J11.2, U7.2
unnamed: J12.2, R20.2
unnamed: J12.3, R21.2
unnamed: J12.4, R22.2
unnamed: R1.1, U1.6
unnamed: R5.2, U2.7
unnamed: R6.2, U2.3
unnamed: R9.1, R10.1, TP7.1
unnamed: R11.1, R12.1, TP14.1
unnamed: R15.1, SW2.2, U3.3
unnamed: R19.2, TP37.1
unnamed: R23.2, TP39.1
unnamed: R29.1, X1.4
unnamed: R33.1, X2.3
unnamed: R34.1, X2.1
unnamed: R35.1, R41.2, U8.8
unnamed: R36.1, U8.1
unnamed: R37.1, U8.4
unnamed: R43.1, U9.13
unnamed: SW1.2, U3.6
unnamed: TP12.1, U1.98
unnamed: TP13.1, U1.99
VCC: C19.2, C20.2, C21.1, D6.1, J1.26, J13.4, R2.1, R3.1, R4.1, R14.1, R24.1, R25.1, R26.1, R27.1, R28.1, R30.2, SW2.1, U3.1, U11.5, U12.5

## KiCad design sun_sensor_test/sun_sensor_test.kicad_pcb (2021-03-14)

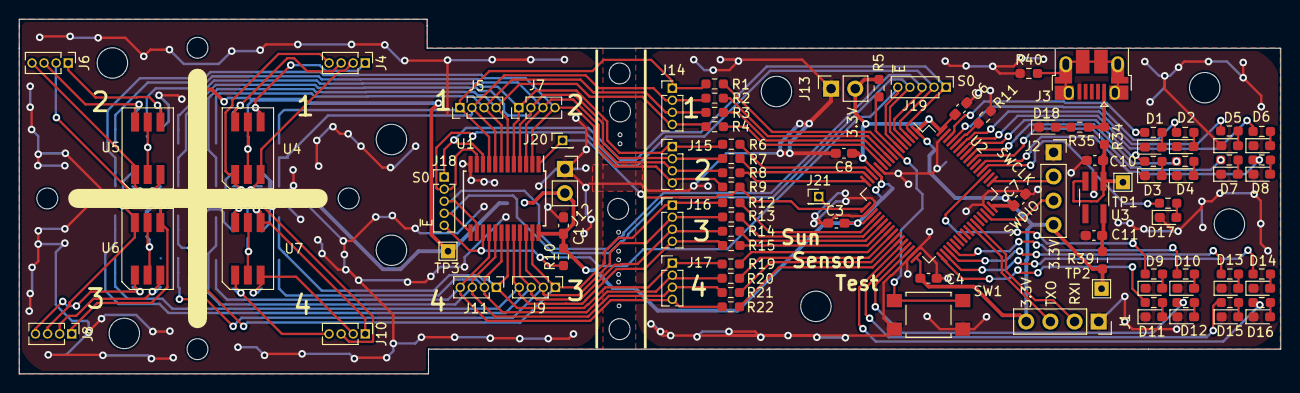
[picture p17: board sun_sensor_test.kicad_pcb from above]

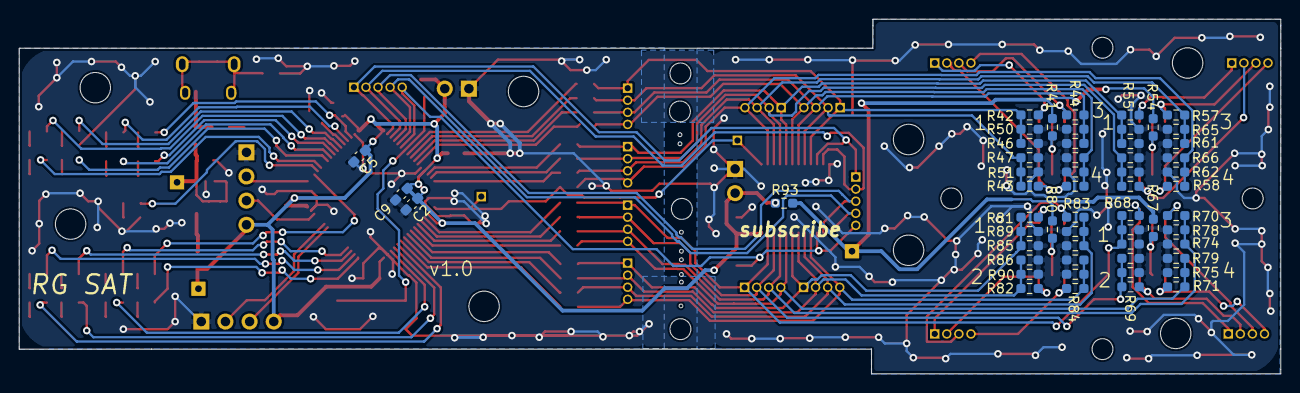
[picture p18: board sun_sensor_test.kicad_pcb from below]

Board: 2 copper layers, 132.7 x 37.3 mm, 178 parts (56 on the bottom side), 105 nets.

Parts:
C1, C2, C3, C4, C5, C6, C7: 0.1uF; C_0603_1608Metric_Pad1.08x0.95mm_HandSolder
C8, C9: 1uF; C_0603_1608Metric_Pad1.08x0.95mm_HandSolder
C10, C11: 4.7uF; C_0603_1608Metric_Pad1.08x0.95mm_HandSolder
D1, D2, D3, D4, D5, D6, D7, D8, D9, D10, D11, D12, D13, D14, D15, D16, D17, D18: RED; LED_0603_1608Metric_Pad1.05x0.95mm_HandSolder
H1, H2, H3, H4, H5, H6, H7, H8: M2 Screw; MountingHole_2.2mm_M2_ISO7380
H9, H10, H11, H12, H13, H14, H15, H16: M3 Screw; MountingHole_3.2mm_M3
H17, H18, H19, H20, H21, H23, H24, H25: mousebite
J1, J2: 2.54mm; PinSocket_1x04_P2.54mm_Vertical
J3: USB_B_Micro; USB_Micro-B_Amphenol_10103594-0001LF_Horizontal
J4, J5, J6, J7, J8, J9, J10, J11, J14, J15, J16, J17: Conn_01x04_Female; PinHeader_1x04_P1.27mm_Vertical
J12, J13: Conn_01x02; PinSocket_1x02_P2.54mm_Vertical
J18, J19: Conn_01x05_Female; PinHeader_1x05_P1.27mm_Vertical
J20, J21: 1.27mm; PinHeader_1x01_P1.27mm_Vertical
R1, R2, R3, R4, R6, R7, R8, R9, R12, R13, R14, R15, R19, R20, R21, R22, R40, R46, R47, R48, R49, R50, R51, R52, R53, R59, R60, R61, R62, R63, R64, R65, R66, R72, R73, R74, R75, R76, R77, R78, R79, R85, R86, R87, R88, R89, R90, R91, R92: DNP; R_0603_1608Metric_Pad0.98x0.95mm_HandSolder
R5, R11: 10K; R_0603_1608Metric_Pad0.98x0.95mm_HandSolder
R10: 100K; R_0603_1608Metric_Pad0.98x0.95mm_HandSolder
R16, R17, R18, R23, R24, R25, R26, R27, R28, R29, R30, R31, R32, R33, R36, R37, R38: 680; R_0603_1608Metric_Pad0.98x0.95mm_HandSolder
R34, R39, R41, R42, R43, R44, R45, R54, R55, R56, R57, R58, R67, R68, R69, R70, R71, R80, R81, R82, R83, R84, R93: 0; R_0603_1608Metric_Pad0.98x0.95mm_HandSolder
R35: 330; R_0603_1608Metric_Pad0.98x0.95mm_HandSolder
SW1: SW_Push; SW_SPST_TL3305A
TP1, TP2, TP3: TP_1.5x1.5; TestPoint_THTPad_1.5x1.5mm_Drill0.7mm
U1: CD74HC4067SM; SSOP-24_5.3x8.2mm_P0.65mm
U2: STM32L051R8Tx; LQFP-64_10x10mm_P0.5mm
U3: ADP150AUJZ-3.3-R7; TSOT-23-5_HandSoldering
U4, U5, U6, U7: K857PE

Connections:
+3V3: C1.1, C2.1, C3.1, C4.1, C5.1, C6.1, C7.1, C8.1, C9.1, J1.4, J2.4, J12.2, J13.2, R5.2, R10.2, R39.2, R93.2, TP2.1, U1.24, U2.1, U2.13, U2.19, U2.32, U2.48, U2.64
+5V: C10.1, R34.2, TP1.1, U3.1, U3.3
/AIN0: R1.1, U2.8
/AIN1: R2.1, U2.9
/AIN2: R3.1, U2.10
/AIN3: R4.1, U2.11
/AIN4: R6.1, U2.14
/AIN5: R7.1, U2.15
/AIN6: R8.1, U2.16
/AIN7: J20.1, J21.1, R9.1, U1.1, U2.17
/AIN8: R12.1, U2.20
/AIN9: R13.1, U2.21
/AIN10: R14.1, U2.22
/AIN11: R15.1, U2.23
/AIN12: R19.1, U2.24
/AIN13: R20.1, U2.25
/AIN14: R21.1, U2.26
/AIN15: R22.1, U2.27
/D1: R16.1, U2.62
/D2: R17.1, U2.61
/D3: R18.1, U2.57
/D4: R23.1, U2.56
/D5: R24.1, U2.59
/D6: R25.1, U2.58
/D7: R26.1, U2.55
/D8: R27.1, U2.53
/D9: R28.1, U2.51
/D10: R29.1, U2.36
/D11: R30.1, U2.33
/D12: R31.1, U2.30
/D13: R32.1, U2.35
/D14: R33.1, U2.34
/D15: R36.1, U2.29
/D16: R37.1, U2.28
/D17: R38.1, U2.52
/K857PE Breakout/A1: J5.1, J14.1, R1.2, R42.1, R46.2, R50.2, U1.9
/K857PE Breakout/A2: J5.2, J14.2, R2.2, R43.1, R47.2, R51.2, U1.8
/K857PE Breakout/A3: J5.3, J14.3, R3.2, R44.1, R48.2, R52.2, U1.7
/K857PE Breakout/A4: J5.4, J14.4, R4.2, R45.1, R49.2, R53.2, U1.6
/K857PE Breakout/VBIAS: R41.1, R54.1, R67.1, R80.1, R93.1, TP3.1
/S0: J18.1, J19.1, U1.10, U2.2
/S1: J18.2, J19.2, U1.11, U2.3
/S2: J18.3, J19.3, U1.14, U2.4
/S3: J18.4, J19.4, U1.13, U2.5
/SWCLK: J2.2, U2.49
/SWDIO: J2.3, U2.46
/USART1_RX: J1.2, U2.43
/USART1_TX: J1.3, U2.42
/sheet60017AC6/A1: J7.1, J15.1, R6.2, R55.1, R59.2, R63.2, U1.5
/sheet60017AC6/A2: J7.2, J15.2, R7.2, R56.1, R60.2, R64.2, U1.4
/sheet60017AC6/A3: J7.3, J15.3, R8.2, R57.1, R61.2, R65.2, U1.3
/sheet60017AC6/A4: J7.4, J15.4, R9.2, R58.1, R62.2, R66.2, U1.2
/sheet60017C33/A1: J9.1, J16.1, R12.2, R68.1, R72.2, R76.2, U1.23
/sheet60017C33/A2: J9.2, J16.2, R13.2, R69.1, R73.2, R77.2, U1.22
/sheet60017C33/A3: J9.3, J16.3, R14.2, R70.1, R74.2, R78.2, U1.21
/sheet60017C33/A4: J9.4, J16.4, R15.2, R71.1, R75.2, R79.2, U1.20
/sheet60017CBC/A1: J11.1, J17.1, R19.2, R81.1, R85.2, R89.2, U1.19
/sheet60017CBC/A2: J11.2, J17.2, R20.2, R82.1, R86.2, R90.2, U1.18
/sheet60017CBC/A3: J11.3, J17.3, R21.2, R83.1, R87.2, R91.2, U1.17
/sheet60017CBC/A4: J11.4, J17.4, R22.2, R84.1, R88.2, R92.2, U1.16
/~E: J18.5, J19.5, R10.1, U1.15, U2.6
GND: C1.2, C2.2, C3.2, C4.2, C5.2, C6.2, C7.2, C8.2, C9.2, C10.2, C11.2, D1.1, D2.1, D3.1, D4.1, D5.1, D6.1, D7.1, D8.1, D9.1, D10.1, D11.1, D12.1, D13.1, D14.1, D15.1, D16.1, D17.1, D18.1, J1.1, J2.1, J3.5, J12.1, J13.1, R11.1, R40.1, R46.1, R47.1, R48.1, R49.1, R50.1, R51.1, R52.1, R53.1, R59.1, R60.1, R61.1, R62.1, R63.1, R64.1, R65.1, R66.1, R72.1, R73.1, R74.1, R75.1, R76.1, R77.1, R78.1, R79.1, R85.1, R86.1, R87.1, R88.1, R89.1, R90.1, R91.1, R92.1, SW1.1, U1.12, U2.12, U2.18, U2.31, U2.47, U2.63, U3.2
unnamed: C11.1, R39.1, U3.5
unnamed: D1.2, R16.2
unnamed: D2.2, R17.2
unnamed: D3.2, R18.2
unnamed: D4.2, R23.2
unnamed: D5.2, R24.2
unnamed: D6.2, R25.2
unnamed: D7.2, R26.2
unnamed: D8.2, R27.2
unnamed: D9.2, R28.2
unnamed: D10.2, R29.2
unnamed: D11.2, R30.2
unnamed: D12.2, R31.2
unnamed: D13.2, R32.2
unnamed: D14.2, R33.2
unnamed: D15.2, R36.2
unnamed: D16.2, R37.2
unnamed: D17.2, R38.2
unnamed: D18.2, R35.2
unnamed: J3.1, R34.1, R35.1
unnamed: J3.6, R40.2
unnamed: J4.1, R42.2, U4.4
unnamed: J4.2, R43.2, U4.3
unnamed: J4.3, R44.2, U4.6
unnamed: J4.4, R45.2, U4.1
unnamed: J6.1, R55.2, U5.4
unnamed: J6.2, R56.2, U5.3
unnamed: J6.3, R57.2, U5.6
unnamed: J6.4, R58.2, U5.1
unnamed: J8.1, R68.2, U6.4
unnamed: J8.2, R69.2, U6.3
unnamed: J8.3, R70.2, U6.6
unnamed: J8.4, R71.2, U6.1
unnamed: J10.1, R81.2, U7.4
unnamed: J10.2, R82.2, U7.3
unnamed: J10.3, R83.2, U7.6
unnamed: J10.4, R84.2, U7.1
unnamed: R5.1, SW1.2, U2.7
unnamed: R11.2, U2.60
unnamed: R41.2, U4.2, U4.5
unnamed: R54.2, U5.2, U5.5
unnamed: R67.2, U6.2, U6.5
unnamed: R80.2, U7.2, U7.5

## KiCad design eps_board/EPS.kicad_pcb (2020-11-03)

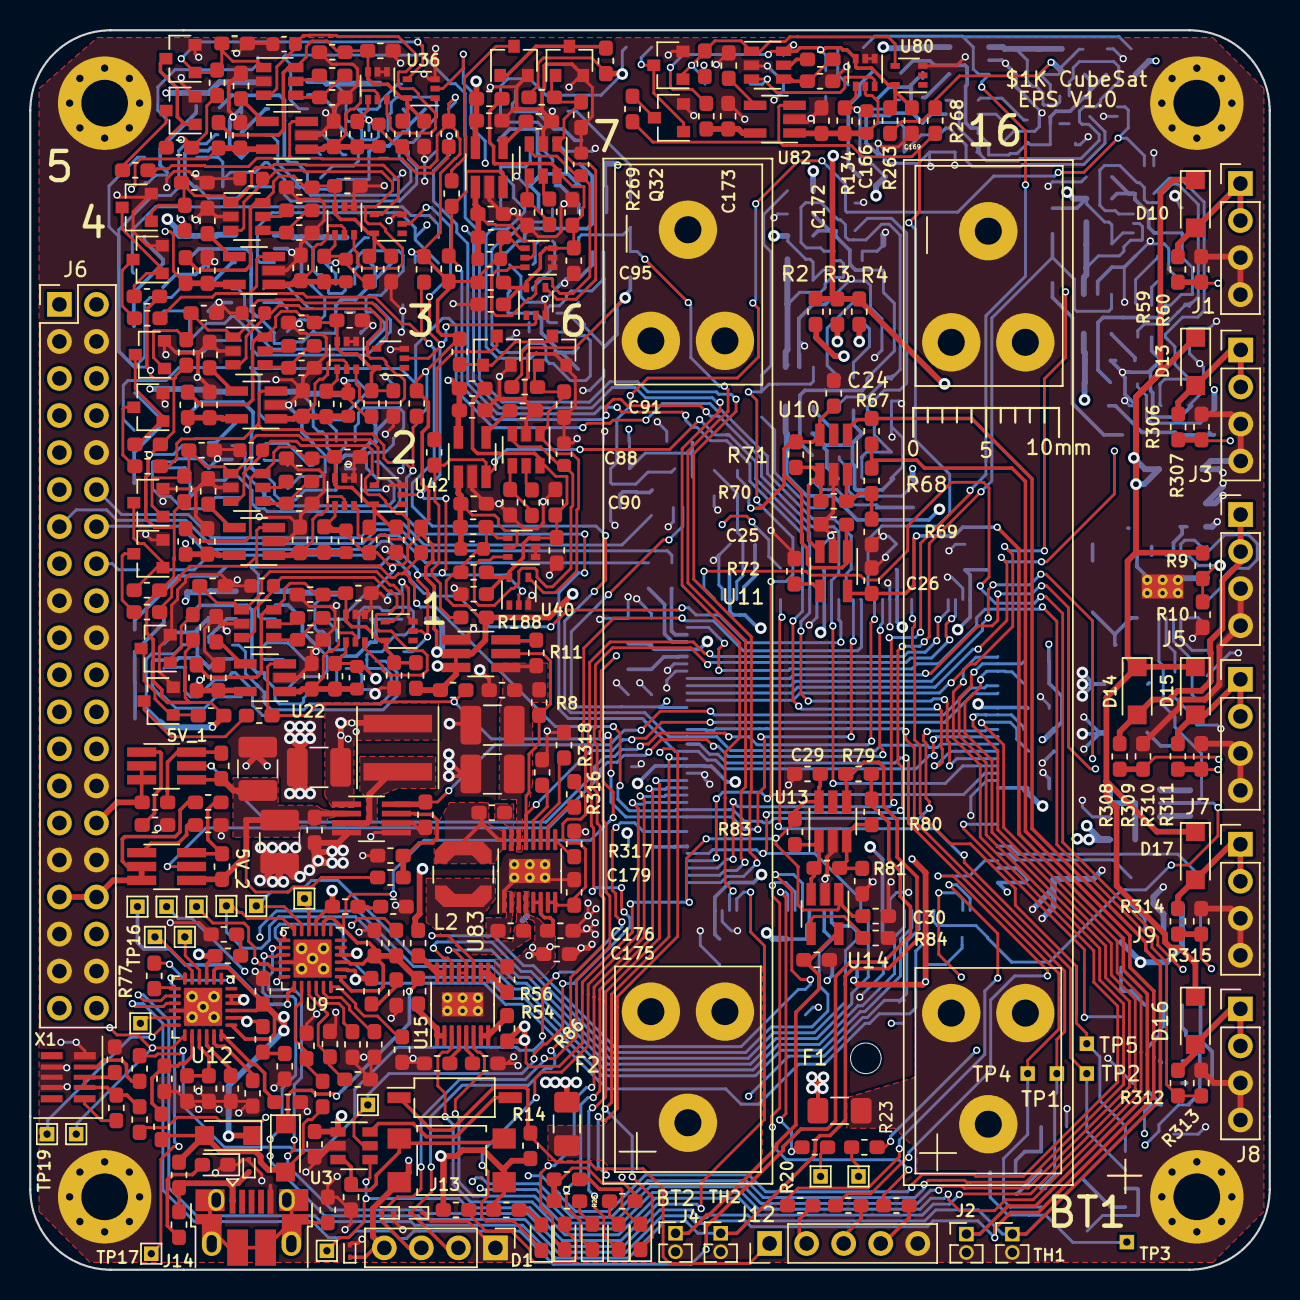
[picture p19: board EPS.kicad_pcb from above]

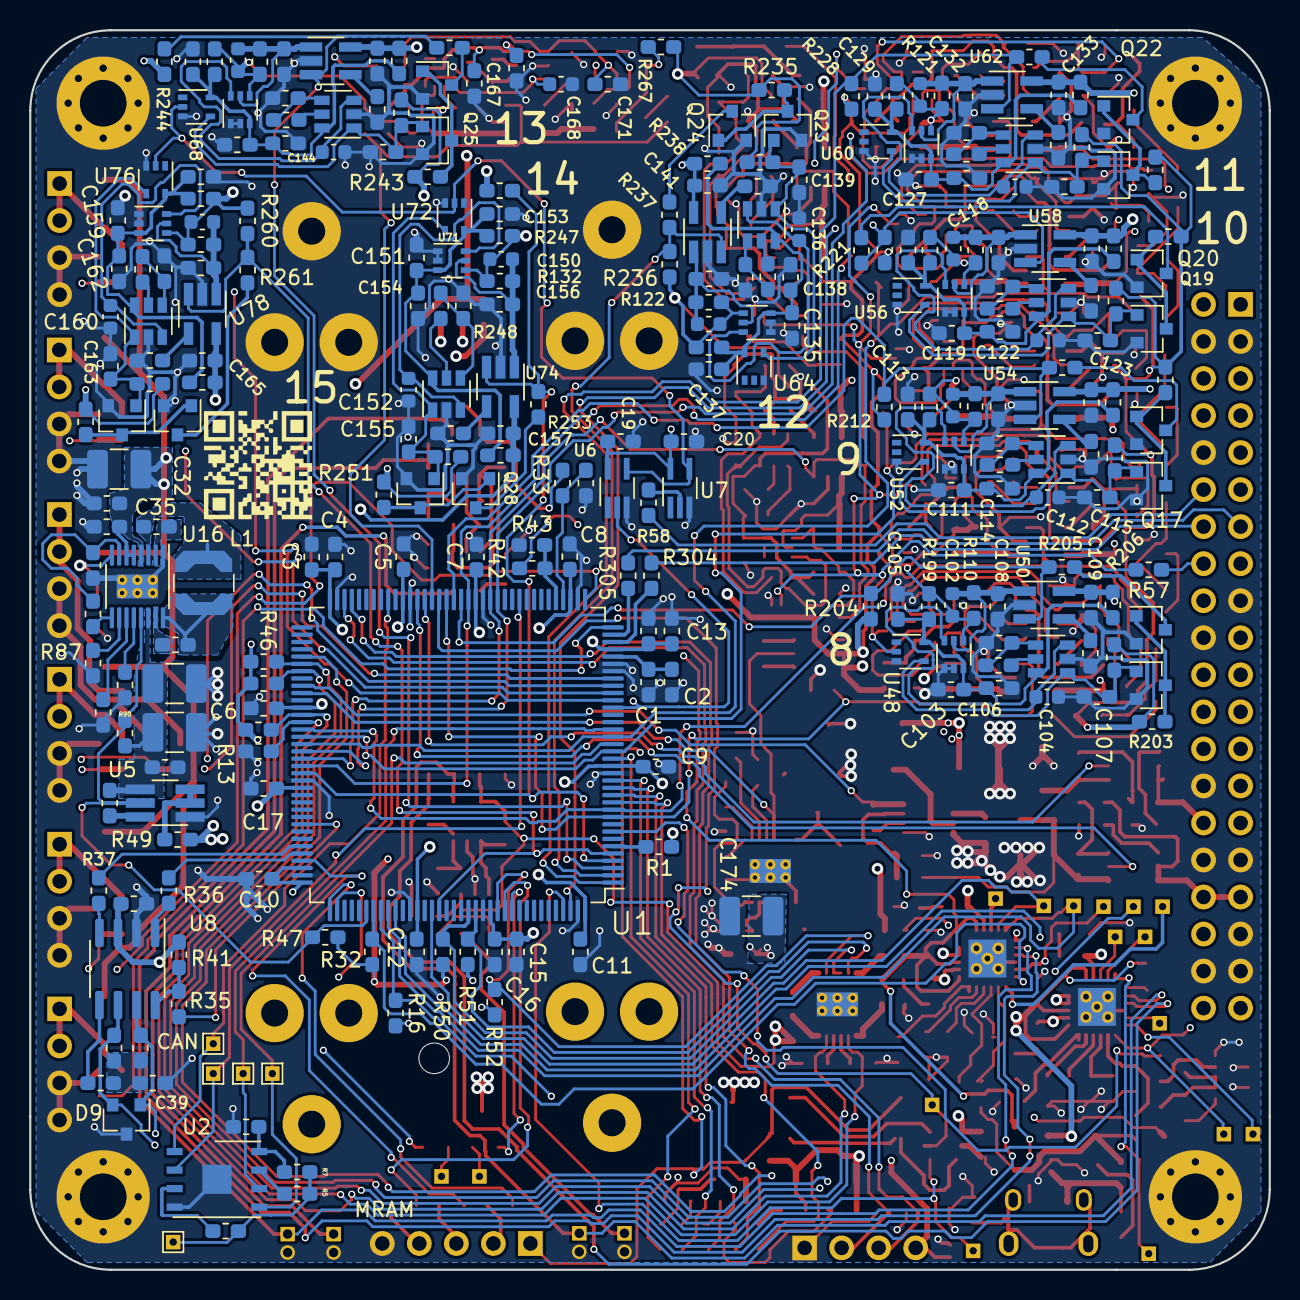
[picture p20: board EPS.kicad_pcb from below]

Board: 4 copper layers, 85.0 x 85.0 mm, 656 parts (279 on the bottom side), 356 nets.

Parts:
BT1, BT2: Battery_Cell; BatteryHolder_Keystone_54_v2_1x18650
C1, C2, C13: 0.01uF; C_0603_1608Metric_Pad1.05x0.95mm_HandSolder
C3, C15, C22, C25, C27, C30, C33, C40, C52, C60, C68, C76, C84, C92, C100, C108, C116, C124, C132, C140, C148, C156, C164, C172, C175, C179, C187, C188, C189, C190, C191, C192: 4.7uF; C_0603_1608Metric_Pad1.05x0.95mm_HandSolder
C4, C5, C6, C7, C8, C9, C10, C11, C12, C16, C17, C18, C19, C20, C21, C24, C26, C29, C31, C36, C38, C47, C49, C50, C53, C55, C57, C58, C61, C63, C65, C66, C69, C71, C73, C74, C77, C79, C81, C82, C85, C87, C89, C90, C93, C95, C97, C98, C101, C103, C105, C106, C109, C111, C113, C114, C117, C119, C121, C122, C125, C127, C129, C130, C133, C135, C137, C138, C141, C143, C145, C146, C149, C151, C153, C154, C157, C159, C161, C162, C165, C167, C169, C170, C173: 0.1uF; C_0603_1608Metric_Pad1.05x0.95mm_HandSolder
C14, C34, C44, C45, C51, C59, C67, C75, C83, C91, C99, C107, C115, C123, C131, C139, C147, C155, C163, C171, C176, C184: 1uF; C_0603_1608Metric_Pad1.05x0.95mm_HandSolder
C23, C28, C43, C182: DNP; C_0603_1608Metric_Pad1.05x0.95mm_HandSolder
C32, C41, C174, C180, C183, C185: 47uF; C_1210_3225Metric_Pad1.42x2.65mm_HandSolder
C35, C37, C177, C178: 22nF; C_0603_1608Metric_Pad1.05x0.95mm_HandSolder
C39: 4.7nF; C_0603_1608Metric_Pad1.05x0.95mm_HandSolder
C42, C181, C186: DNP; C_1210_3225Metric_Pad1.42x2.65mm_HandSolder
C46, C48, C54, C56, C62, C64, C70, C72, C78, C80, C86, C88, C94, C96, C102, C104, C110, C112, C118, C120, C126, C128, C134, C136, C142, C144, C150, C152, C158, C160, C166, C168: DNP; C_0603_1608Metric
D1, D19: LED_SMD_RED; LED_0603_1608Metric_Pad1.05x0.95mm_HandSolder
D2: LED_SMD_GREEN; LED_0603_1608Metric_Pad1.05x0.95mm_HandSolder
D3, D4, D5: LED_SMD_YELLOW; LED_0603_1608Metric_Pad1.05x0.95mm_HandSolder
D6, D7, D8, D18: ESD9B5.0ST5G; D_SOD-923
D9: NUP2105L; SOT-23
D10, D11, D12, D13, D14, D15, D16, D17: NRVB120VLSFT1G; D_SOD-123FL_handsolder
F1, F2: Polyfuse; Fuse_1206_3216Metric_Pad1.42x1.75mm_HandSolder
FID4: Fiducial; Gauge_10mm_Type1_SilkScreenTop
H1: MountingHole; MountingHole_2.1mm
H2, H3, H4, H5: MountingHole_Pad; MountingHole_3.2mm_M3_Pad_Via
J1, J3, J5, J7, J8, J9: Conn_01x04; PinHeader_1x04_P2.54mm_Vertical
J2, J4: Conn_01x02_Female; PinHeader_1x02_P1.27mm_Vertical
J6: Conn_02x20_Odd_Even; PinHeader_2x20_P2.54mm_Vertical
J12: Conn_01x05; PinHeader_1x05_P2.54mm_Vertical
J13: Conn_01x04_Male; PinHeader_1x04_P2.54mm_Vertical
J14: USB_B_Micro; USB_Micro-B_Amphenol_10103594-0001LF_Horizontal
L1, L2: 4.7uH; L_Coilcraft_LPS4018
L3: 2.2uH; L_Coilcraft_XAL5030
Q1, Q2, Q3, Q4, Q5, Q6, Q7, Q8, Q9, Q10, Q11, Q12, Q13, Q14, Q15, Q16, Q17, Q18, Q19, Q20, Q21, Q22, Q23, Q24, Q25, Q26, Q27, Q28, Q29, Q30, Q31, Q32: 2N7002K; SOT-23
R1, R29, R30, R31, R35, R36, R37, R38, R57, R58, R87, R88, R89, R90, R143, R149, R151, R157, R159, R165, R167, R173, R175, R181, R183, R189, R191, R197, R199, R205, R207, R213, R215, R221, R223, R229, R231, R237, R239, R245, R247, R253, R255, R261, R263, R269, R304, R305, R316, R317, R318, R319, R327: 0; R_0603_1608Metric_Pad1.05x0.95mm_HandSolder
R2, R3, R4, R7, R49, R53, R54, R55, R56, R328: 10m; R_0603_1608Metric_Pad1.05x0.95mm_HandSolder
R5, R6, R8, R10, R12, R13, R14, R16, R17, R18, R32, R33, R41, R42, R46, R47, R50, R51, R52, R59, R60, R65, R68, R77, R80, R144, R152, R160, R168, R176, R184, R192, R200, R208, R216, R224, R232, R240, R248, R256, R264, R306, R307, R308, R309, R310, R311, R312, R313, R314, R315, R320: 100K; R_0603_1608Metric_Pad1.05x0.95mm_HandSolder
R9: 224K; R_0603_1608Metric_Pad1.05x0.95mm_HandSolder
R11, R48, R62, R64, R66, R67, R74, R76, R78, R79, R97, R98: 10K; R_0603_1608Metric_Pad1.05x0.95mm_HandSolder
R15: 8.85K; R_0603_1608Metric_Pad1.05x0.95mm_HandSolder
R19, R20, R21, R22, R23: 49.9; R_0603_1608Metric_Pad1.05x0.95mm_HandSolder
R24, R25, R26, R27, R28, R329: 330; R_0603_1608Metric_Pad1.05x0.95mm_HandSolder
R34, R43: 150K; R_0603_1608Metric_Pad1.05x0.95mm_HandSolder
R39, R40: 60.4; R_0603_1608Metric_Pad1.05x0.95mm_HandSolder
R61, R73: 26.7K; R_0603_1608Metric_Pad1.05x0.95mm_HandSolder
R63, R71, R75, R83, R145, R147, R148, R153, R155, R156, R161, R163, R164, R169, R171, R172, R177, R179, R180, R185, R187, R188, R193, R195, R196, R201, R203, R204, R209, R211, R212, R217, R219, R220, R225, R227, R228, R233, R235, R236, R241, R243, R244, R249, R251, R252, R257, R259, R260, R265, R267, R268, R321: 1M; R_0603_1608Metric_Pad1.05x0.95mm_HandSolder
R69, R81: 280K; R_0603_1608Metric_Pad1.05x0.95mm_HandSolder
R70, R82, R150, R158, R166, R174, R182, R190, R198, R206, R214, R222, R230, R238, R246, R254, R262, R270: DNP; R_0603_1608Metric_Pad1.05x0.95mm_HandSolder
R72, R84, R100, R102, R104, R106, R112, R114, R116, R118, R124, R126, R128, R130, R136, R138, R140, R142: 3.09K; R_0603_1608Metric_Pad1.05x0.95mm_HandSolder
R85, R86: 150; R_0603_1608Metric_Pad1.05x0.95mm_HandSolder
R91, R92: 1K; R_0603_1608Metric_Pad1.05x0.95mm_HandSolder
R93, R95, R96, R107, R108, R109, R110, R119, R120, R121, R122, R131, R132, R133, R134: 0.1; R_0603_1608Metric_Pad1.05x0.95mm_HandSolder
R94: 0.039; R_0603_1608Metric_Pad1.05x0.95mm_HandSolder
R99: 20K; R_0603_1608Metric_Pad1.05x0.95mm_HandSolder
R101, R103, R105, R123, R125, R127, R129, R135, R137, R139, R141: 140K; R_0603_1608Metric_Pad1.05x0.95mm_HandSolder
R111, R117: 698K; R_0603_1608Metric_Pad1.05x0.95mm_HandSolder
R113, R115: 1.5M; R_0603_1608Metric_Pad1.05x0.95mm_HandSolder
R322: 137K; R_0603_1608Metric_Pad1.05x0.95mm_HandSolder
R323, R324, R325, R326: 1; R_0603_1608Metric_Pad1.05x0.95mm_HandSolder
SW1: SW_DIP_x01; SW_DIP_SPSTx01_Slide_Copal_CHS-01B_W7.62mm_P1.27mm
SW2: SW_Push; SW_SPST_TL3305A
TH1, TH2: Thermistor_NTC; PinHeader_1x02_P1.27mm_Vertical
TP1, TP2, TP3, TP4, TP5, TP8, TP9: TP_smt_1x1; TestPoint_THTPad_1.0x1.0mm_Drill0.5mm
TP7, TP10, TP11, TP12, TP13, TP14, TP15, TP16, TP17, TP18, TP19, TP20: TP_1x1; TestPoint_THTPad_1.0x1.0mm_Drill0.5mm
TP37, TP39: TP_1.5x1.5; TestPoint_THTPad_1.0x1.0mm_Drill0.5mm
U1: STM32L496ZGTx; LQFP-144_20x20mm_P0.5mm
U2: MR25H10; DFN-8-1EP_6x5mm_P1.27mm_EP2x2mm
U3: TPL5010; SOT-23-6
U4, U5, U17, U18: TPS270; TSOT-23-6_HandSoldering
U6, U7: 74LVC1G07; SOT-353_SC-70-5_Handsoldering
U8: SN65HVD230; SOIC-8_3.9x4.9mm_P1.27mm
U9, U12: LTC4066; QFN-24-1EP_4x4mm_P0.5mm_EP2.6x2.6mm_0.4mmThermalVias
U10, U13: MCP65R46; SOT-23-6_Handsoldering
U11, U14, U22, U26, U30, U34, U38, U42, U46, U50, U54, U58, U62, U66, U70, U74, U78, U82: FPF2123; SOT-23-5_HandSoldering
U15: LTC4415; MSOP-16-1EP_3x4.039mm_P0.5mm_EP1.651x2.845mm_0.3mmThermalVi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
U16, U83: LTC3130-1; MSOP-16-1EP_3x4.039mm_P0.5mm_EP1.651x2.845mm_0.3mmThermalVi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
U19, U23, U27, U31, U35, U39, U43, U47, U51, U55, U59, U63, U67, U71, U75, U79: NCS211; SOT-363_SC-70-6
U20, U24, U28, U32, U36, U40, U44, U48, U52, U56, U60, U64, U68, U72, U76, U80: 74LVC1G07; SOT-353_SC-70-5
U21, U25, U29, U33, U37, U41, U45, U49, U53, U57, U61, U65, U69, U73, U77, U81: MCP65R46; SOT-23-6
U84: MP3414A; TSOT-23-8_HandSoldering
X1: TG-3541CE; Oscillator_SMD_SeikoEpson_TG3541CE-10Pin_3.2x2.5mm_HandSold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

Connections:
+3V3: C19.2, C20.2, C46.2, C54.2, C62.2, C70.2, C78.2, C86.2, C94.2, C102.2, C110.2, C118.2, C126.2, C134.2, C142.2, C150.2, C158.2, C166.2, R93.2, R94.2, R95.2, R96.2, R107.2, R108.2, R109.2, R110.2, R119.2, R120.2, R121.2, R122.2, R131.2, R132.2, R133.2, R134.2, R143.2, R145.2, R147.2, R148.2, R151.2, R153.2, R155.2, R156.2, R159.2, R161.2, R163.2, R164.2, R167.2, R169.2, R171.2, R172.2, R175.2, R177.2, R179.2, R180.2, R183.2, R185.2, R187.2, R188.2, R191.2, R193.2, R195.2, R196.2, R199.2, R201.2, R203.2, R204.2, R207.2, R209.2, R211.2, R212.2, R215.2, R217.2, R219.2, R220.2, R223.2, R225.2, R227.2, R228.2, R231.2, R233.2, R235.2, R236.2, R239.2, R241.2, R243.2, R244.2, R247.2, R249.2, R251.2, R252.2, R255.2, R257.2, R259.2, R260.2, R263.2, R265.2, R267.2, R268.2, U4.2, U4.3, U6.5, U7.5, U19.4, U23.4, U27.4, U31.4, U35.4, U39.4, U43.4, U47.4, U51.4, U55.4, U59.4, U63.4, U67.4, U71.4, U75.4, U79.4
+5V: C184.1, C185.1, C186.1, R97.2, R98.2, R321.2, U17.4, U18.4, U84.2
/3.3V_9: C117.2, J6.9, R214.1, U54.5
/3.3V_10: C125.2, J6.6, R222.1, U58.5
/3.3V_11: C133.2, J6.1, R230.1, U62.5
/3.3V_12: C141.2, J6.18, R238.1, U66.5
/3.3V_16: C173.2, R270.1, U82.5
/3.3V_ACS_LOGIC: C85.2, J6.2, R182.1, U38.5
/3.3V_AVI_CAN: C77.2, J6.5, R174.1, U34.5
/3.3V_CLK: C109.2, J6.25, R206.1, U50.5
/3.3V_EPS_CAN: C38.1, C157.2, R41.1, R254.1, U8.3, U74.5
/3.3V_EPS_MRAM: C165.2, R5.1, R6.1, R7.2, R262.1, TP3.1, U78.5
/3.3V_EPS_STM: C21.1, C149.2, D6.1, J13.4, R2.1, R3.1, R4.1, R12.2, R14.1, R16.2, R18.2, R24.1, R25.1, R26.1, R27.1, R28.1, R30.2, R32.2, R46.2, R47.2, R50.1, R51.1, R52.1, R246.1, SW2.1, U3.1, U70.5
/3.3V_GPS: C61.2, J6.24, R158.1, U26.5
/3.3V_GYRO: C93.2, J6.23, R190.1, U42.5
/3.3V_MAG: C101.2, J6.8, R198.1, U46.5
/3.3V_MRAM: C69.2, J6.11, R166.1, U30.5
/3.3V_STM_CORE: C53.2, J6.26, R150.1, U22.5
/5V0_1: C44.1, J6.30, U17.2, U17.3
/5V0_2: C45.1, J6.33, J6.34, U18.2, U18.3
/AVI_EXTRN_RST: R57.2, U20.2, U24.2, U28.2, U32.2, U36.2, U40.2, U44.2, U48.2
/BATTERY/NTC: R67.2, TH1.1, U9.14, U10.4
/BATTERY/VNTC: R67.1, R68.1, U9.15
/BATTERY_CHARGER/BAT: C189.1, F1.1, U9.2, U9.4, U9.5
/BC_1_CLDIS: TP7.1, U9.10
/BC_1_ISTAT: R66.2, U9.24
/BC_1_POL: R46.1, TP12.1, U1.78, U9.19
/BC_1_SHDN: TP11.1, U1.117, U9.12
/BC_1_SUSP: TP10.1, U1.123, U9.11
/BC_2_CLDIS: TP15.1, U12.10
/BC_2_ISTAT: R78.2, U12.24
/BC_2_POL: R18.1, TP18.1, U1.79, U12.19
/BC_2_SHDN: TP17.1, U1.118, U12.12
/BC_2_SUSP: TP16.1, U1.77, U12.11
/CANH: D9.1, J6.40, R39.1, U8.7
/CANL: D9.2, J6.39, R40.2, U8.6
/CURRENT_MONITORS/PWR1_8_ON: R204.1, R205.1, U1.54, U50.3
/CURRENT_MONITORS/PWR1_9_ON: R212.1, R213.1, U1.55, U54.3
/CURRENT_MONITORS/PWR1_10_ON: R220.1, R221.1, U1.142, U58.3
/CURRENT_MONITORS/PWR1_11_ON: R228.1, R229.1, U1.1, U62.3
/CURRENT_MONITORS/PWR1_12_ON: R236.1, R237.1, U1.2, U66.3
/CURRENT_MONITORS/PWR1_13_ON: R244.1, R245.1, U1.3, U70.3
/CURRENT_MONITORS/PWR1_16_ON: R268.1, R269.1, U1.58, U82.3
/CURRENT_MONITORS/PWR2_1_ON: U1.59, U17.5
/CURRENT_MONITORS/PWR2_2_ON: U1.60, U18.5
/CURRENT_MONITORS/RST1_13: U6.4, U7.4, U68.2, U72.2, U76.2
/CURRENT_MONITORS/sheet601A160D/ISET+: R100.2, U22.4
/CURRENT_MONITORS/sheet601A160D/RREF+: R99.2, U21.5
/CURRENT_MONITORS/sheet601A160D/RREF-: R99.1, R144.2, U21.4
/CURRENT_MONITORS/sheet601A160D/SHUNT-: C46.1, C52.2, R93.1, U19.5, U22.1
/CURRENT_MONITORS/sheet620B1C5A/ISET+: R138.2, U74.4
/CURRENT_MONITORS/sheet620B1C5A/RREF+: R137.2, U73.5
/CURRENT_MONITORS/sheet620B1C5A/RREF-: R137.1, R248.2, U73.4
/CURRENT_MONITORS/sheet620B1C5A/SHUNT-: C150.1, C156.2, R132.1, U71.5, U74.1
/CURRENT_MONITORS/sheet620B1C5B/ISET+: R140.2, U78.4
/CURRENT_MONITORS/sheet620B1C5B/RREF+: R139.2, U77.5
/CURRENT_MONITORS/sheet620B1C5B/RREF-: R139.1, R256.2, U77.4
/CURRENT_MONITORS/sheet620B1C5B/SHUNT-: C158.1, C164.2, R133.1, U75.5, U78.1
/CURRENT_MONITORS/sheet620B1C5C/ISET+: R142.2, U82.4
/CURRENT_MONITORS/sheet620B1C5C/RREF+: R141.2, U81.5
/CURRENT_MONITORS/sheet620B1C5C/RREF-: R141.1, R264.2, U81.4
/CURRENT_MONITORS/sheet620B1C5C/SHUNT-: C166.1, C172.2, R134.1, U79.5, U82.1
/CURRENT_MONITORS/sheet620B1C59/ISET+: R136.2, U70.4
/CURRENT_MONITORS/sheet620B1C59/RREF+: R135.2, U69.5
/CURRENT_MONITORS/sheet620B1C59/RREF-: R135.1, R240.2, U69.4
/CURRENT_MONITORS/sheet620B1C59/SHUNT-: C142.1, C148.2, R131.1, U67.5, U70.1
/CURRENT_MONITORS/sheet6206D7D7/ISET+: R106.2, U34.4
/CURRENT_MONITORS/sheet6206D7D7/RREF+: R105.2, U33.5
/CURRENT_MONITORS/sheet6206D7D7/RREF-: R105.1, R168.2, U33.4
/CURRENT_MONITORS/sheet6206D7D7/SHUNT-: C70.1, C76.2, R96.1, U31.5, U34.1
/CURRENT_MONITORS/sheet6209BA5A/ISET+: R128.2, U62.4
/CURRENT_MONITORS/sheet6209BA5A/RREF+: R127.2, U61.5
/CURRENT_MONITORS/sheet6209BA5A/RREF-: R127.1, R224.2, U61.4
/CURRENT_MONITORS/sheet6209BA5A/SHUNT-: C126.1, C132.2, R121.1, U59.5, U62.1
/CURRENT_MONITORS/sheet6209BA5B/ISET+: R130.2, U66.4
/CURRENT_MONITORS/sheet6209BA5B/RREF+: R129.2, U65.5
/CURRENT_MONITORS/sheet6209BA5B/RREF-: R129.1, R232.2, U65.4
/CURRENT_MONITORS/sheet6209BA5B/SHUNT-: C134.1, C140.2, R122.1, U63.5, U66.1
/CURRENT_MONITORS/sheet6209BA58/ISET+: R124.2, U54.4
/CURRENT_MONITORS/sheet6209BA58/RREF+: R123.2, U53.5
/CURRENT_MONITORS/sheet6209BA58/RREF-: R123.1, R208.2, U53.4
/CURRENT_MONITORS/sheet6209BA58/SHUNT-: C110.1, C116.2, R119.1, U51.5, U54.1
/CURRENT_MONITORS/sheet6209BA59/ISET+: R126.2, U58.4
/CURRENT_MONITORS/sheet6209BA59/RREF+: R125.2, U57.5
/CURRENT_MONITORS/sheet6209BA59/RREF-: R125.1, R216.2, U57.4
/CURRENT_MONITORS/sheet6209BA59/SHUNT-: C118.1, C124.2, R120.1, U55.5, U58.1
/CURRENT_MONITORS/sheet62057B58/ISET+: R104.2, U30.4
/CURRENT_MONITORS/sheet62057B58/RREF+: R103.2, U29.5
/CURRENT_MONITORS/sheet62057B58/RREF-: R103.1, R160.2, U29.4
/CURRENT_MONITORS/sheet62057B58/SHUNT-: C62.1, C68.2, R95.1, U27.5, U30.1
/CURRENT_MONITORS/sheet6204228E/ISET+: R102.2, U26.4
/CURRENT_MONITORS/sheet6204228E/RREF+: R101.2, U25.5
/CURRENT_MONITORS/sheet6204228E/RREF-: R101.1, R152.2, U25.4
/CURRENT_MONITORS/sheet6204228E/SHUNT-: C54.1, C60.2, R94.1, U23.5, U26.1
/CURRENT_MONITORS/sheet6208477B/ISET+: R112.2, U38.4
/CURRENT_MONITORS/sheet6208477B/RREF+: R111.2, U37.5
/CURRENT_MONITORS/sheet6208477B/RREF-: R111.1, R176.2, U37.4
/CURRENT_MONITORS/sheet6208477B/SHUNT-: C78.1, C84.2, R107.1, U35.5, U38.1
/CURRENT_MONITORS/sheet6208477C/ISET+: R114.2, U42.4
/CURRENT_MONITORS/sheet6208477C/RREF+: R113.2, U41.5
/CURRENT_MONITORS/sheet6208477C/RREF-: R113.1, R184.2, U41.4
/CURRENT_MONITORS/sheet6208477C/SHUNT-: C86.1, C92.2, R108.1, U39.5, U42.1
/CURRENT_MONITORS/sheet6208477D/ISET+: R116.2, U46.4
/CURRENT_MONITORS/sheet6208477D/RREF+: R115.2, U45.5
/CURRENT_MONITORS/sheet6208477D/RREF-: R115.1, R192.2, U45.4
/CURRENT_MONITORS/sheet6208477D/SHUNT-: C94.1, C100.2, R109.1, U43.5, U46.1
/CURRENT_MONITORS/sheet6208477E/ISET+: R118.2, U50.4
/CURRENT_MONITORS/sheet6208477E/RREF+: R117.2, U49.5
/CURRENT_MONITORS/sheet6208477E/RREF-: R117.1, R200.2, U49.4
/CURRENT_MONITORS/sheet6208477E/SHUNT-: C102.1, C108.2, R110.1, U47.5, U50.1
/EPS_EXTRN_RST: R58.2, U7.2
/EPS_WATCHDOG: J12.1, R14.2, SW1.1, U1.25, U6.2
/HPWR_EN: R320.2, U1.81, U84.8
/IDEAL_EN1: R12.1, U1.85, U15.3
/INTERBOARD_CONNECTOR/AVI_RESET: J6.16, R57.1
/INTERBOARD_CONNECTOR/EPS_RESET: J6.12, R58.1
/PG_3V3: R8.1, U1.82, U4.5, U83.13
/PG_SOLAR: R17.1, R47.1, U1.114, U5.5, U16.13
/PMIC/ADC1_IN9: R33.2, R34.2, U1.40
/PMIC/ADC1_IN10: R42.2, R43.2, U1.41
/PMIC/CAN1_RX: R37.2, U1.103
/PMIC/CAN1_TX: R36.2, U1.104
/PMIC/CAN_RS: R35.2, U1.100
/PMIC/CAN_TRANSCEIVER/Vref: R38.2, U8.5
/PMIC/INT_1: R148.1, R149.1, U1.10, U1.56, U22.3
/PMIC/INT_2: R156.1, R157.1, U1.11, U1.87, U26.3
/PMIC/INT_3: R164.1, R165.1, U1.19, U1.88, U30.3
/PMIC/INT_4: R172.1, R173.1, U1.21, U1.89, U34.3
/PMIC/INT_5: R180.1, R181.1, U1.49, U1.90, U38.3
/PMIC/INT_6: R188.1, R189.1, U1.50, U1.91, U42.3
/PMIC/INT_7: R196.1, R197.1, U1.53, U1.92, U46.3
/PMIC/INT_8: R252.1, R253.1, U1.4, U1.93, U74.3
/PMIC/INT_9: R260.1, R261.1, U1.5, U1.124, U78.3
/PMIC/JTCK_SWCLK: R20.1, U1.109
/PMIC/JTDI: R23.1, U1.110
/PMIC/JTDO_TRACESWO: R22.1, U1.133
/PMIC/JTMS_SWDIO: R21.1, U1.105
/PMIC/LED_1: D1.1, U1.12
/PMIC/LED_2: D2.1, U1.13
/PMIC/LED_3: D3.1, U1.14
/PMIC/LED_4: D4.1, U1.15
/PMIC/LED_5: D5.1, U1.18
/PMIC/LPUART1_RX: D8.2, J13.2, U1.69
/PMIC/LPUART1_TX: D7.2, J13.3, U1.70
/PMIC/NJRST: R19.1, U1.134
/PMIC/OSC32_TCXO/OE: R31.1, X1.1
/PMIC/QUADSPI_BK1_IO0: TP4.1, U1.20, U2.5
/PMIC/QUADSPI_BK1_IO1: TP2.1, U1.46, U2.2
/PMIC/QUADSPI_BK1_NCS: TP5.1, U1.64, U2.1
/PMIC/QUADSPI_CLK: TP1.1, U1.22, U2.6
/PMIC/RCC_OSC32_IN: R29.2, U1.8
/PMIC/UART4_RX: R305.2, U1.35
/PMIC/UART4_TX: R304.2, U1.34
/PMIC/WATCHDOG_DONE: TP9.1, U1.141, U3.4
/PMIC/WATCHDOG_WAKE: TP8.1, U1.57, U3.5
/SOLAR_5V: C187.1, C190.1, R49.1, U9.9, U12.9
/SOLAR_ADC1: R59.2, R60.1, U1.26
/SOLAR_ADC2: R306.2, R307.1, U1.27
/SOLAR_ADC3: R308.2, R309.1, U1.28
/SOLAR_ADC4: R310.2, R311.1, U1.29
/SOLAR_ADC5: R312.2, R313.1, U1.36
/SOLAR_ADC6: R314.2, R315.1, U1.37
/SOLAR_MPPT_5V/MPPC: R9.2, R10.2, U16.8
/SOLAR_MPPT_5V/VCC: C40.1, R88.2, U16.7
/SOLAR_MPPT_5V/VOUT: C41.1, C42.1, C43.1, R17.2, R48.2, U5.4, U16.14
/UART_RXI: J6.13, R305.1
/UART_TXO: J6.14, R304.1
/VEXT: D11.2, D12.2, R61.2, R73.2, R328.1
/VOUT1: C24.1, C25.1, C188.1, D11.1, R33.1, R53.2, R65.2, R71.1, U9.1, U9.3, U9.8, U10.6, U11.1
/VOUT2: C29.1, C30.1, C191.1, D12.1, R42.1, R54.2, R77.2, R83.1, U12.1, U12.3, U12.8, U13.6, U14.1
/VRAW_SOLAR: C32.1, C33.1, C34.1, D10.1, D13.1, D14.1, D15.1, D16.1, D17.1, R9.1, U16.4, U16.5, U16.6
/sheet5F4CFCDE/BAT: C192.1, F2.1, U12.2, U12.4, U12.5
/sheet5F4CFCDE/NTC: R79.2, TH2.1, U12.14, U13.4
/sheet5F4CFCDE/VNTC: R79.1, R80.1, U12.15
/sheet5F71F776/VIN1: R53.1, U15.1, U15.2
/sheet5F71F776/VIN2: R54.1, U15.7, U15.8
/sheet5F71F776/VOUT1: R55.2, U15.15, U15.16
/sheet5F71F776/VOUT2: R56.2, U15.9, U15.10
/sheet5FCD3934/MPPC: C179.1, R316.2, U83.7, U83.8
/sheet5FCD3934/VOUT: C180.1, C181.1, C182.1, R8.2, R11.2, U4.4, U83.14
/~BC_1_CHRG: R32.1, TP13.1, U1.115, U9.18
/~BC_1_VEXT: TP14.1, U9.17
/~BC_2_CHRG: R16.1, TP19.1, U1.116, U12.18
/~BC_2_VEXT: TP20.1, U12.17
/~IDEAL_EN2: R13.2, U1.86, U15.6
/~IDEAL_STATUS1: R51.2, U1.129, U15.14
/~IDEAL_STATUS2: R52.2, U1.132, U15.11
/~IDEAL_WARN1: R50.2, U1.128, U15.12, U15.13
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

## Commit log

2020-08-30 Initial EPS. Each solar input has a regulator.
    [BATTERY.sch, BATTERY_CHARGER.sch, EPS.kicad_pcb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]
2020-08-30 EPS with schottky diodes & 1 regulator
    [BATTERY.sch, BATTERY_CHARGER.sch, EPS.sch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]
2020-08-30 Removed unecessary footprint lib
    [OSC32_TCXO.sch, OSC_HSE_TCXO.sch, SD_CARD.sch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]
2020-10-09 Progress on EPS
    [ACS.sch, AVIONICS_BOARD.sch, BATTERY.sch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]
2020-10-16 Essentially done with EPS schematic
    [ACS.sch, AVIONICS_BOARD.sch, BATTERY.sch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]
2020-10-28 EPS layout in progress
    [BATTERY.sch, CURRENT_MONITOR.sch, EPS.kicad_pcb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]
2020-11-03 EPS V1.0 Complete
    [BATTERY.sch, BATTERY_CHARGER.sch, CURRENT_MONITOR.sch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]
2021-03-14 Sun Sensor Test board
    [k857pe.sch, sun_sensor_test.kicad_pcb, sun_sensor_test.sch]
2021-03-19 Update Avionics part names to match KiCad update. Update Avionics board to use new interboard connector
    [ACS.sch, CAN_TRANSCEIVER.sch, DEBUG_INTERFACE.sch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]
2021-04-30 Avionics Board layout done
    [ACS.sch, AVIONICS_BOARD.kicad_pcb, GYRO.sch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]
2021-10-17 Radio Schematic update complete.
2021-12-18 Add EPS & Avionics BOM
    [AVIONICS_BOARD_grouped.csv, EPS_v1_0_BOM.csv]
